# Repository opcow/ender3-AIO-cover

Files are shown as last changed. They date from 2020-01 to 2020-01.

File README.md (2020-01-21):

# Ender 3 Electronics Case Cover

#### An alternative cover for the [Ender 3 all in one, universal rear electronics case](https://www.thingiverse.com/thing:3688967) design by [teaching tech](https://youtu.be/k83M5H796U8).

Designed to fit my Ender 3 Pro. On the regular Ender 3 there would be a small gap between the cover and the Y axis rail.

Teaching tech's design is really nice. I just wasn't super happy with the cover. This alternative cover features a separable hinge. When raised the cover can be completely removed for easier access to the electronics. I can remove it in seconds without moving/turning my printer. (There is an optional remix of TT's melzi case which moves the borad to the left a bit and removes the TL smoother mounts.)

The hinge piece slides onto the end of 40x40 extrusion. Before sliding the hinge on, you will need to remove the endcap from the extrusion and you will also need to slide the electronics case partially out because the stop that the cover rest on hangs lower than the back wall of the case.

To install the cover, pull the buildplate carriage forward for clearance then insert the 'J' shaped side of the cover into the hinge slot with the cover at about a 60 degree angle. The cover is not meant to be a tight fit on the case. It hovers a couple of MM above it. If you have any wires that run over the 40x40 extrusion under the bed, slide the cover back enough that you don't pinch them when lowering it into place.

The slotted version of the cover accepts trays and spacers and can be used with a 40 mm or 50 mm fan. The trays come in 10 mm and 5 mm deep versions. If you have clerance over heatsinks you can use a 10 mm one so that the top of the fan is flush with the top of the cover.

All models are oriented the way I print them. I use supports on the trays. I printed hinge.stl standing on end with a brim, but it would probably print ok without the brim if you have good build plate adhesion. You may need to trim, scrape, or sand the underside of the 'J' as there may be a slight ridge there after printing (I scraped mine using a razor blade).

| Files | Descrition |
| --- | --- |
| 40mm_cover.stl | Full cover for 40mm fan. |
| 40mm_mount.stl | Mount for 40mm fan. |
| 40x10_tray.stl | 10 mm deep tray for 40 mm fan (for use with the slotted cover). |
| 40x5_tray.stl | 5 mm deep tray for 40 mm fan (for use with the slotted cover). |
| 50mm_cover.stl | Full cover for 40mm fan. |
| 50mm_mount.stl | Mount for 50mm fan. |
| 50x10_tray.stl | 10 mm deep tray for 50 mm fan (for use with the slotted cover). |
| 50x5_tray.stl | 5 mm deep tray for 50 mm fan (for use with the slotted cover). |
| hinge.stl | Cover hinge mounts to the 40x40 extrustion (all covers and mounts use this). |
| slotted_cover.stl | An adjustable cover. Tray fit into the slot. Use spacers to position the fan. |
| solid_cover.stl | A cover with no fan mount. |
| 10mm_spacer.stl | Spacer for use with the slotted cover and tray. Use 2 with the 50 mm tray or 3 with the 40 mm tray. |
| melzi_case.stl | Remix of TT's case, moving the board to the left for better access. |
| rear_cap.stl | Fits the top of the rear wall of the case. Holds the wire bundle in and gives a landing for the cover. |

---

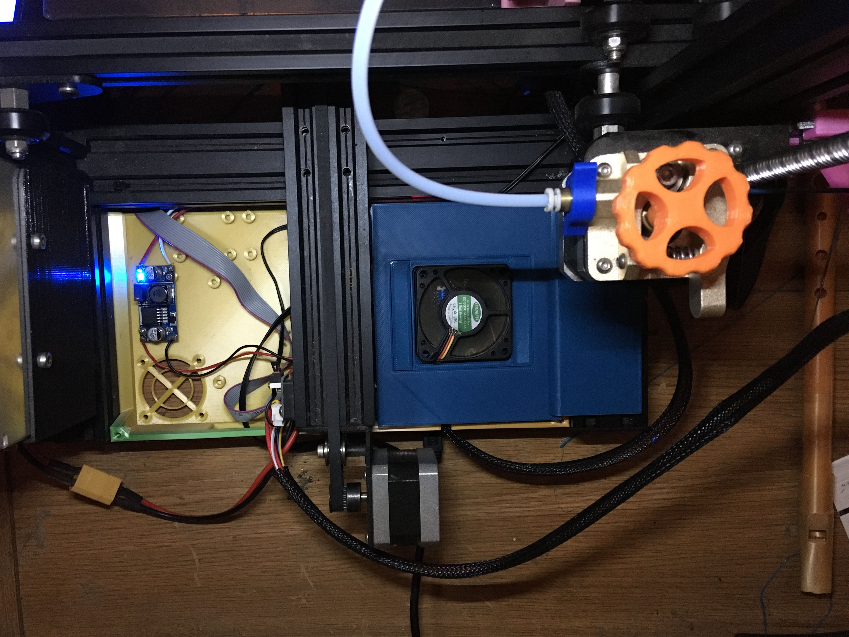
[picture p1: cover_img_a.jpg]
view 1 image

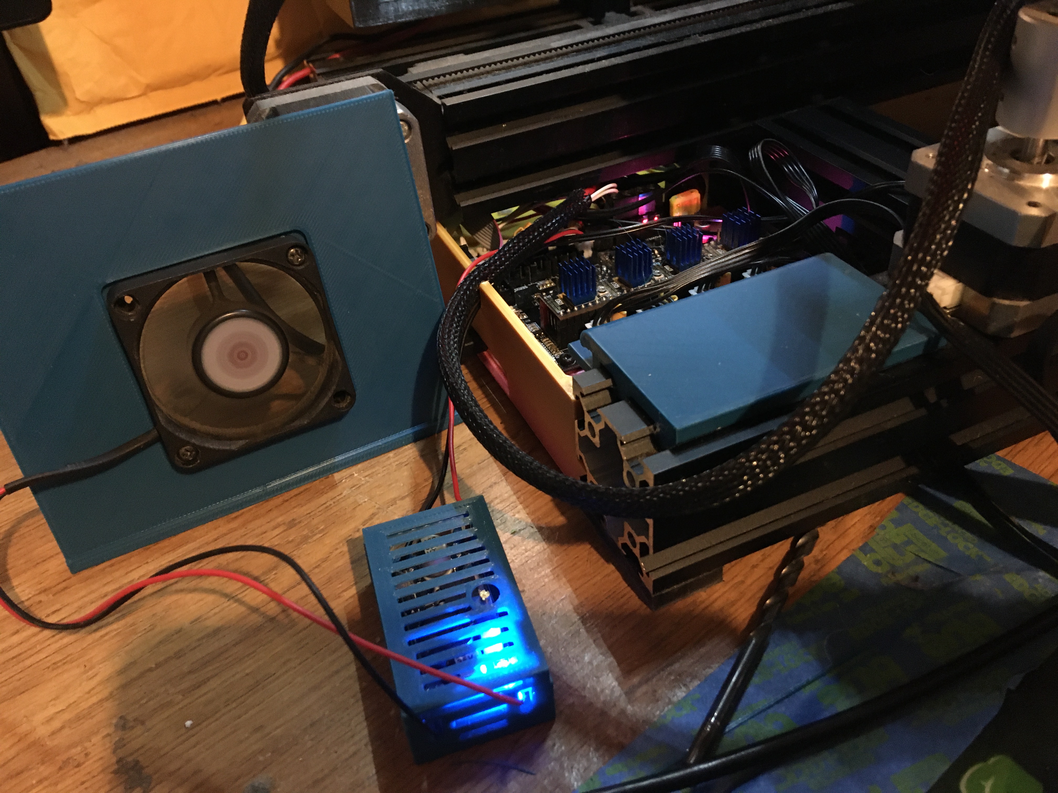
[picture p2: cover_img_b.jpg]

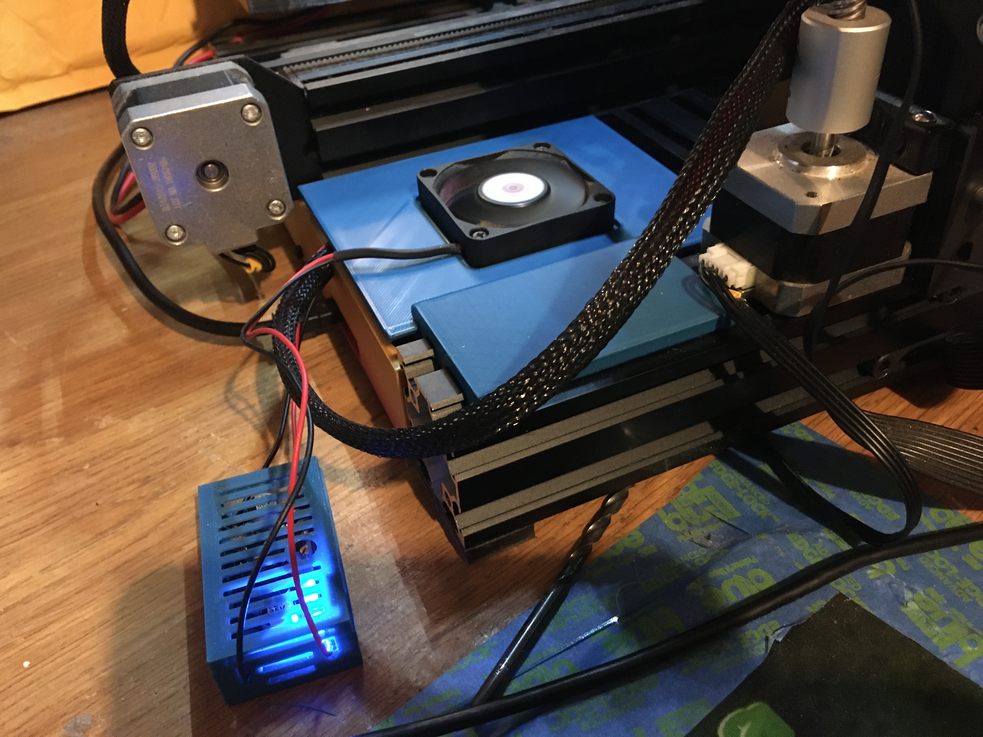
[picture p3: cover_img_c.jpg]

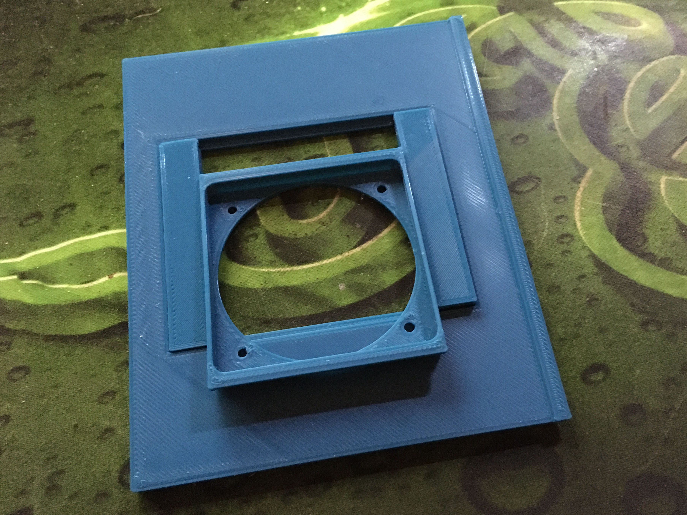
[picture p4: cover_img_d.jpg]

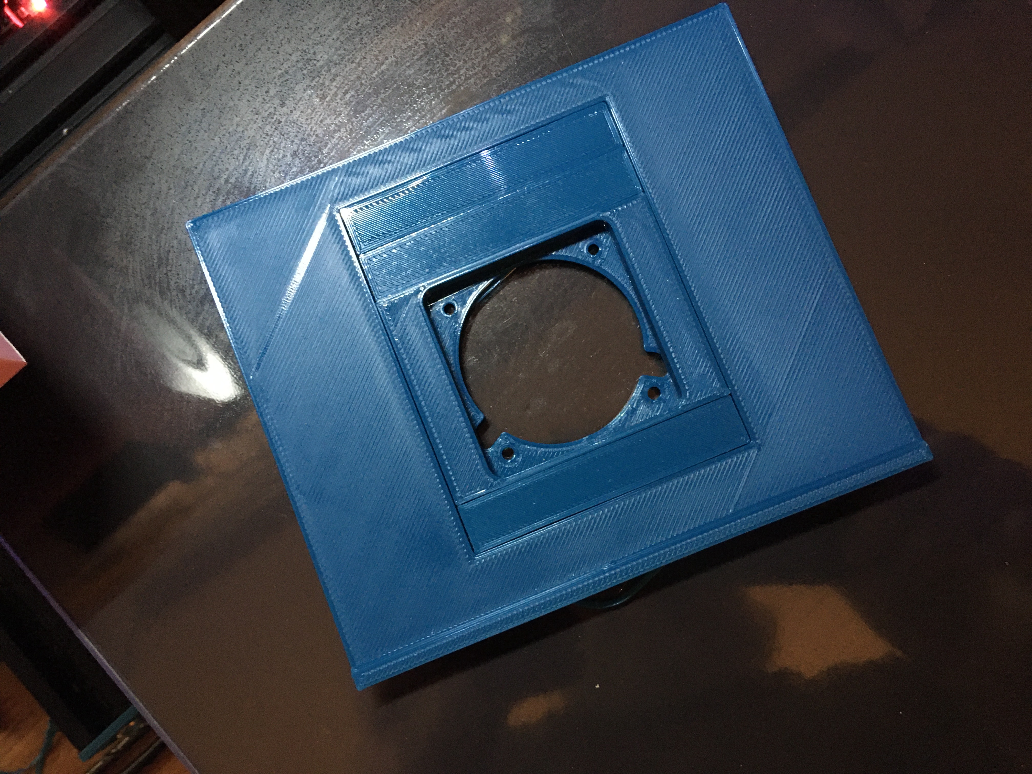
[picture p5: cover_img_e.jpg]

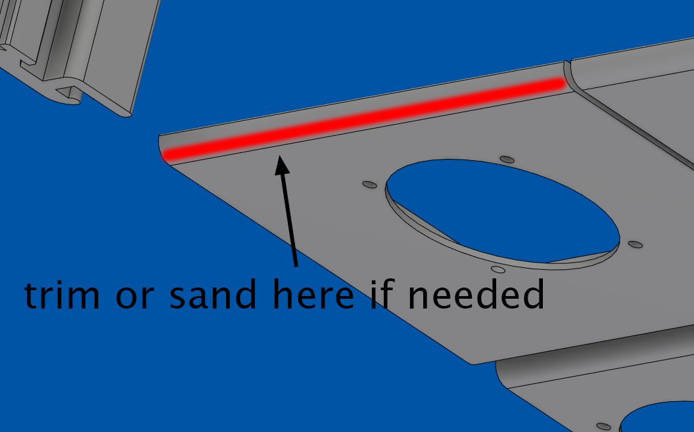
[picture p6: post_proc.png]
post processing image


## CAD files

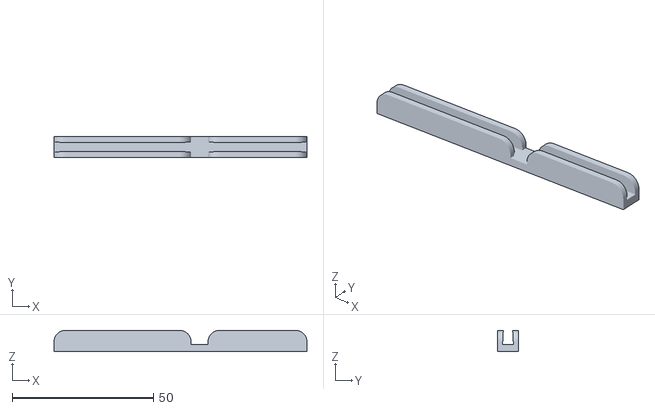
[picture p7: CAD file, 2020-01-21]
rear_cap.stl
89.5 x 7.30 x 7.50

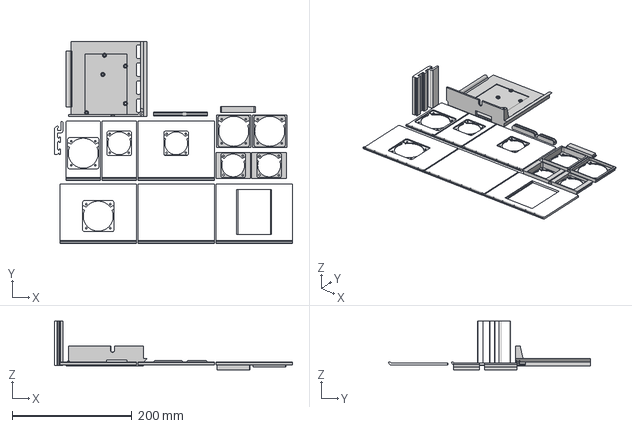
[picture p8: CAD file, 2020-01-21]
cover_with_hinge.step
397.0 x 336.6 x 81.7 mm

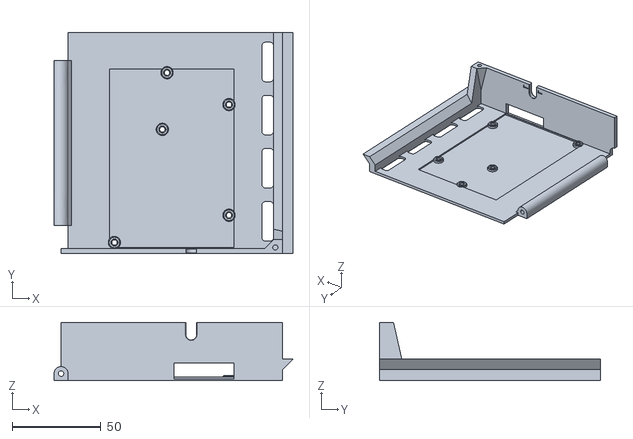
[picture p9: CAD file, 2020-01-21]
melzi_case.stl
135.0 x 125.0 x 33.0

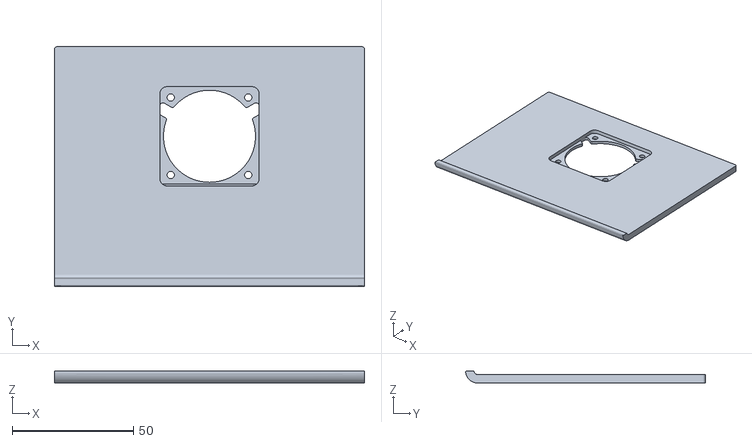
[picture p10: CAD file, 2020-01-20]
40mm_cover.stl
128.0 x 99.0 x 5.00

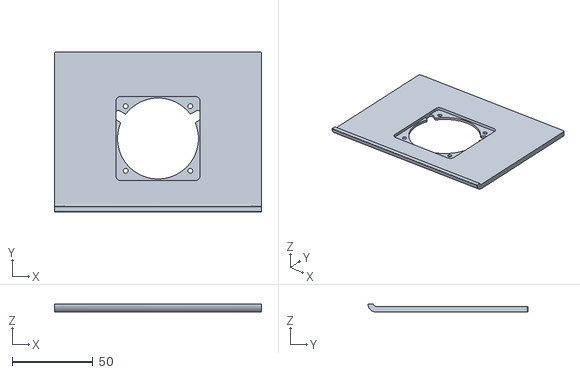
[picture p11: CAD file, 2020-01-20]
50mm_cover.stl
128.0 x 99.0 x 5.00

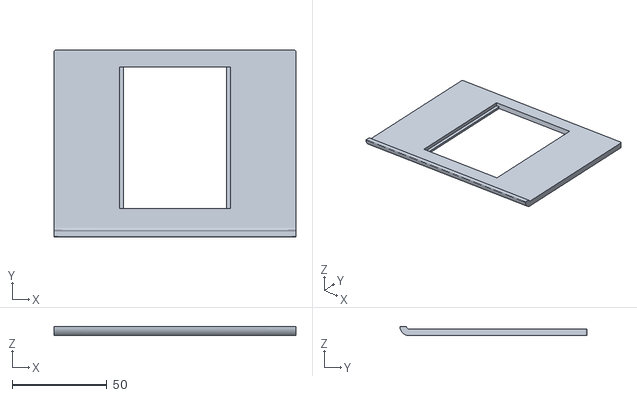
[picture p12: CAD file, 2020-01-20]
slotted_cover.stl
128.0 x 99.0 x 5.00

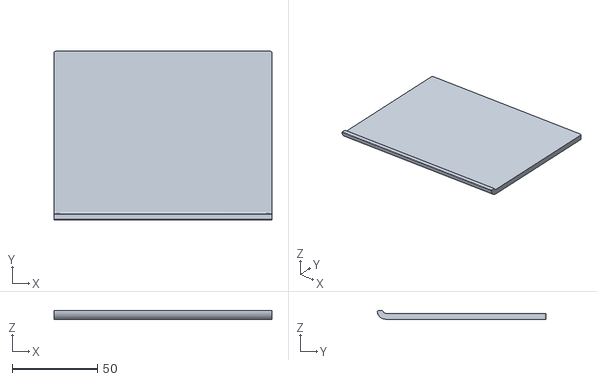
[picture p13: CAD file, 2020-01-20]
solid_cover.stl
128.0 x 99.0 x 5.00

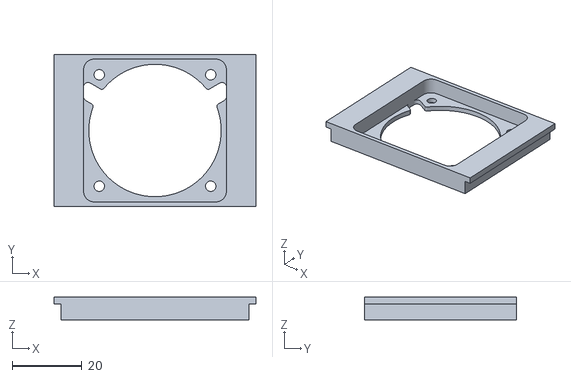
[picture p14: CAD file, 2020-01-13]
40x5_tray.stl
58.0 x 43.7 x 6.50

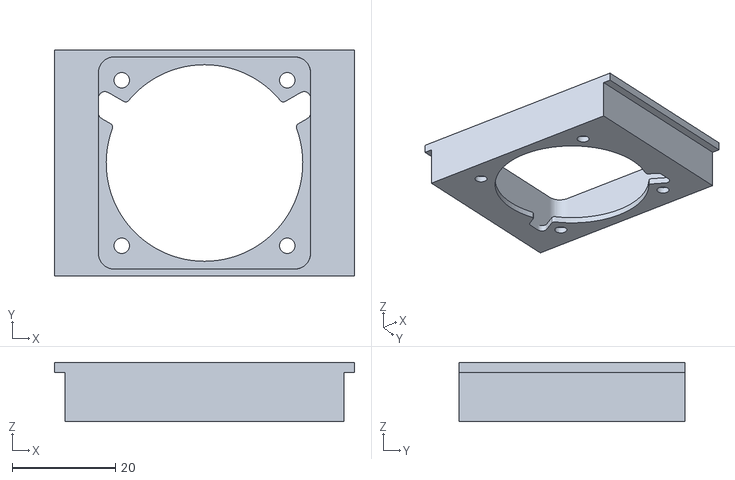
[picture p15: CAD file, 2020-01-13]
40x10_tray.stl
58.0 x 43.7 x 11.5

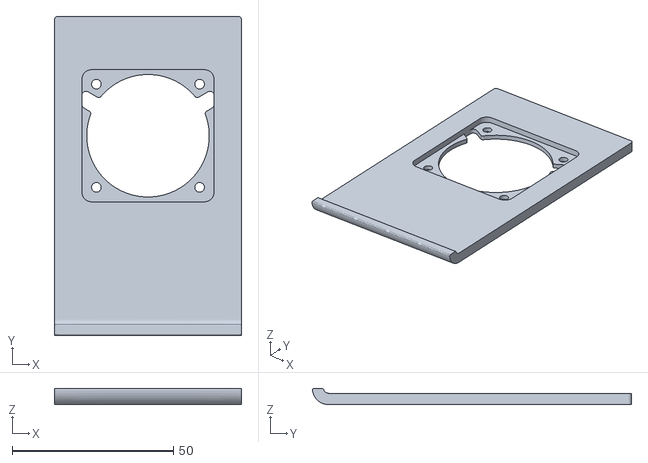
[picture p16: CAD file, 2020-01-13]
40mm_mount.stl
58.0 x 99.0 x 5.00

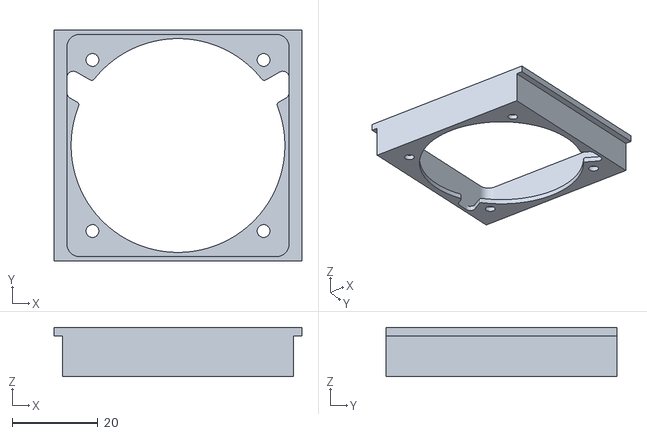
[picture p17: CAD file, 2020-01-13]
50x10_tray.stl
58.0 x 54.0 x 11.5

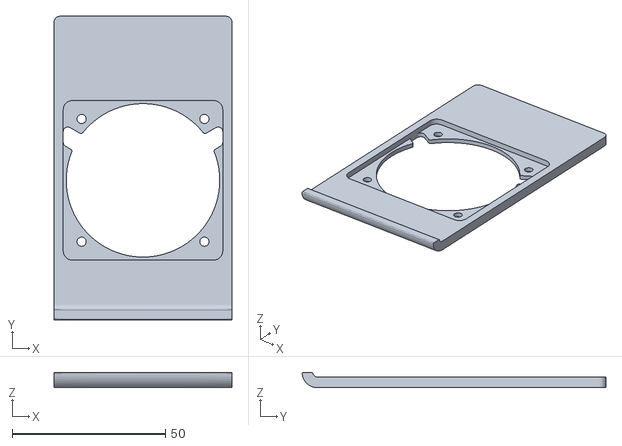
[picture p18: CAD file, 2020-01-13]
50mm_mount.stl
58.0 x 99.0 x 5.00

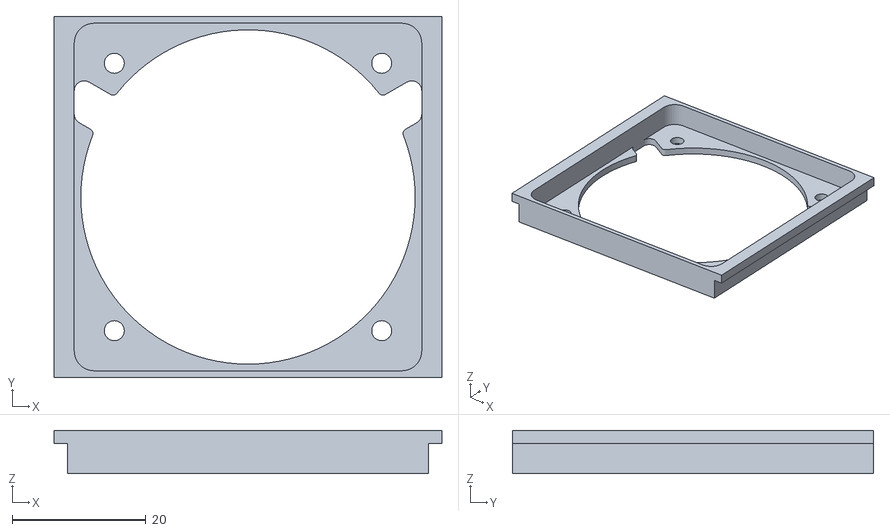
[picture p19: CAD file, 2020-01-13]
50x5_tray.stl
58.0 x 54.0 x 6.50

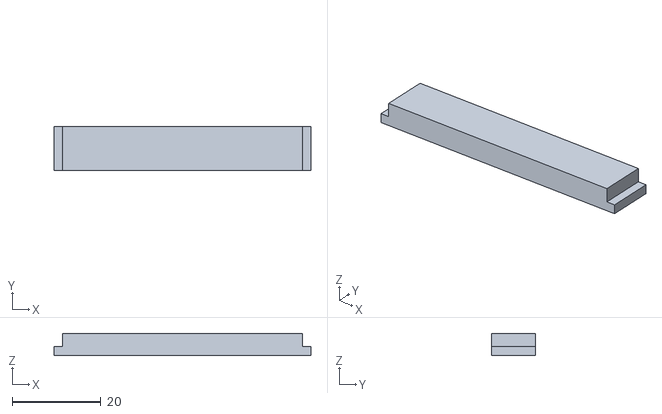
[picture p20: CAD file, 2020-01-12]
10mm_spacer.stl
58.0 x 10.0 x 5.00

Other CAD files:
hinge.stl

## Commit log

2020-01-11 hello, world
    [cover.stl, cover_with_hinge.f3d, cover_with_hinge.step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]
2020-01-11 alternate covers
    [cover.stl, fan_mount.stl, solid_cover.stl]
2020-01-11 add 40mm fan options
    [40mm_cover.stl, 40mm_mount.stl, 50mm_cover.stl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]
2020-01-11 update CAD files
    [cover.stl, fan_mount.stl]
2020-01-11 fix faces on 40mm parts
    [40mm_cover.stl, 40mm_mount.stl, cover_with_hinge.f3d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]
2020-01-12 adjustable fan position options
    [40x10_tray.stl, 40x5_tray.stl, 50x10_tray.stl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]
2020-01-12 removed left/right lip
    [cover_with_hinge.f3d, cover_with_hinge.step, solid_cover.stl]
2020-01-12 thicken walls on 40mm trays
    [40x10_tray.stl, 40x5_tray.stl, cover_with_hinge.f3d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]
2020-01-12 slotted cover and spacer image
2020-01-13 added cutout for wire egress
    [40mm_cover.stl, 40mm_mount.stl, 40x10_tray.stl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]
2020-01-13 installation and printing details
2020-01-13 resized 40 mm tray
    [10mm_spacer.stl, 40x10_tray.stl, 40x5_tray.stl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]
2020-01-13 10 mm spacer description
2020-01-20 increased cover widths 10 mm
    [40mm_cover.stl, 50mm_cover.stl, cover_with_hinge.f3d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]
2020-01-21 added left case remix
    [cover_with_hinge.step, melzi_case.stl, rear_cap.stl]
2020-01-21 info re melizi case
2020-01-21 trimmed height
    [rear_cap.stl]
